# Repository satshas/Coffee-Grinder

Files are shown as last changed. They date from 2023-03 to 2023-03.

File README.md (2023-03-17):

# Coffee-Grinder
An Open Source Coffe Grinder made with a Pop-up Factory and Open Hardware Fab Lab Machines
<br>
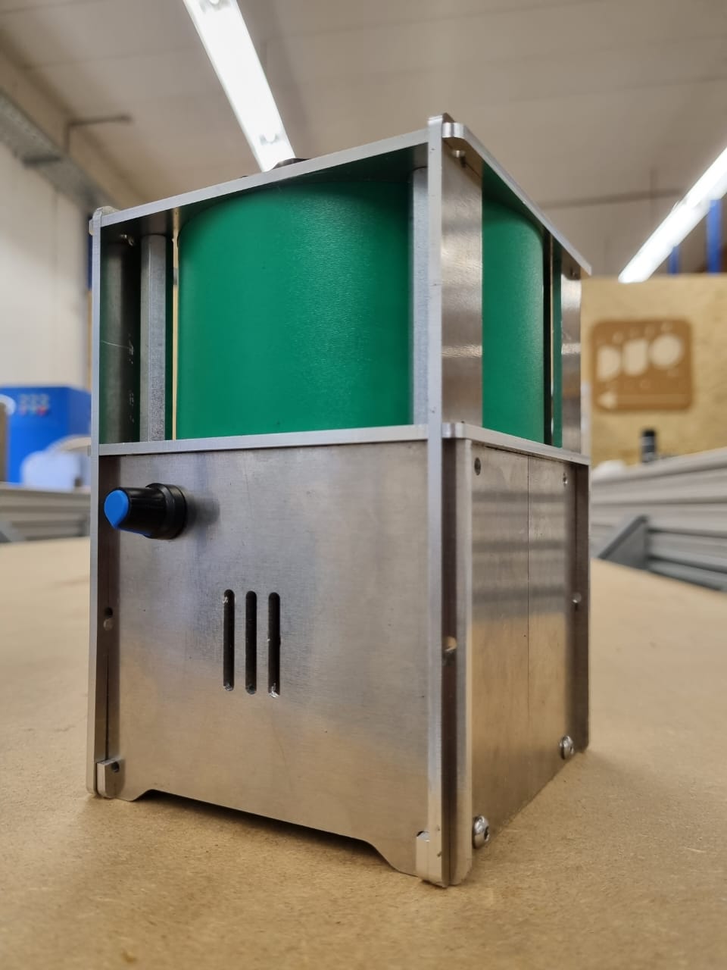
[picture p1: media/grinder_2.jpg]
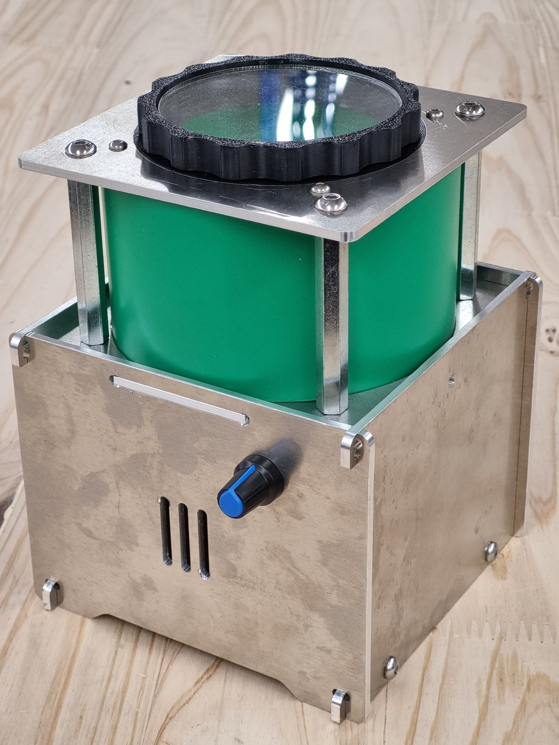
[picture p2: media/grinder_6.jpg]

<div align="center">      Version 1  |  Version 2</div>
<br>

# Specifications

- CNC milled 3mm aluminum housing
- 12V 775 DC Motor
- CNC milled grinding blade with bending
- adjustable speed
- grinding time: about 1 minute
- 3D printed screwable cap
- laser cut polypropylene grinding area

# Assembly Instructions V2

## **Sub Assembly A: grinding chamber**
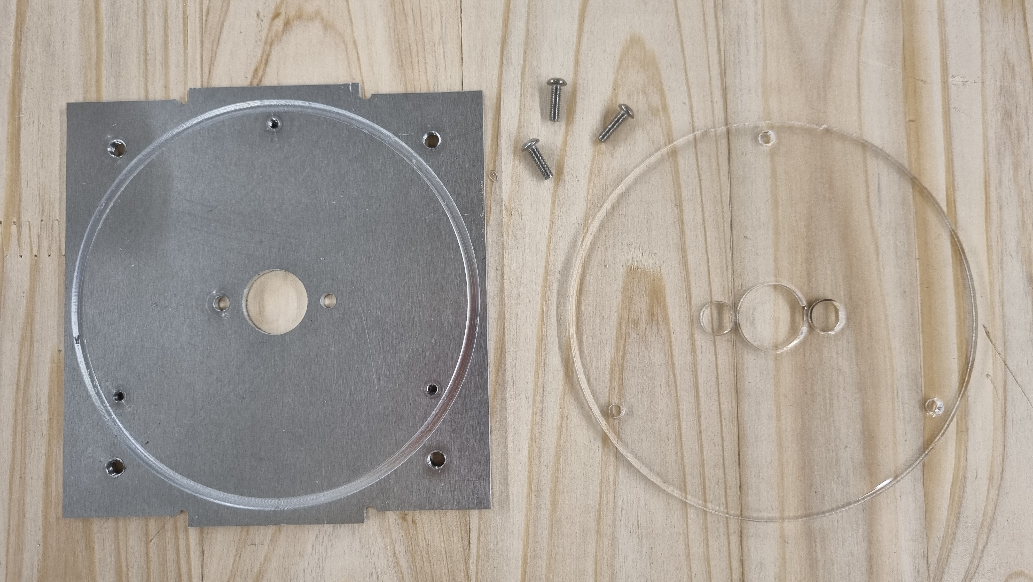
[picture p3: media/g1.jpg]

<br>
1. Attach big acrylic disc to aluminium square with 3 central holes using M3x10mm bolts (this assabled part will be refered in the next steps as "botom of the grinding chamber").
<br><br>
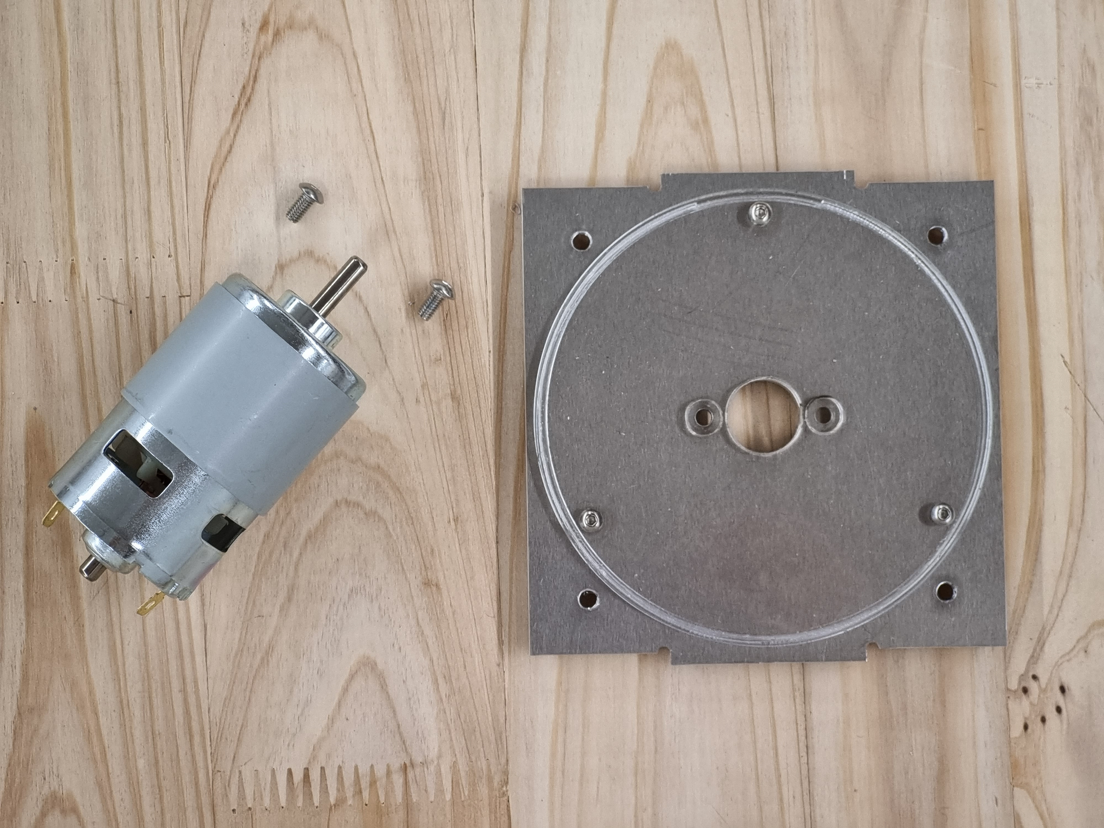
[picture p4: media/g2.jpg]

<br>
2. Attach the DC motor to the bottom ginding chamber using 2 M4x10 bolts.
<br><br>
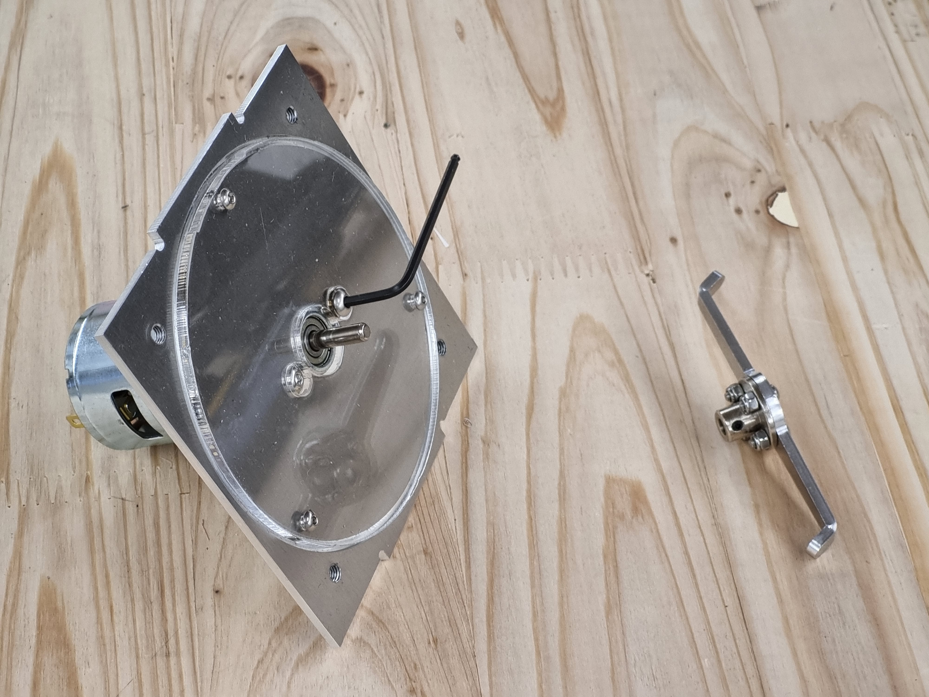
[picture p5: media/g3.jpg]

<br>


<div align="center">The blade should be assembled to the motor coupler using 4 M3x10mm bolts and 4 M3 Locknuts.<br>To secure the motor coupler to the motor´s shaft you need to tighten  the 2 setscrews.</div>
<br><br>
3. Attach the male part of the M5x60mm standoffs to the bottom ob the grinding chamber.<br><br>
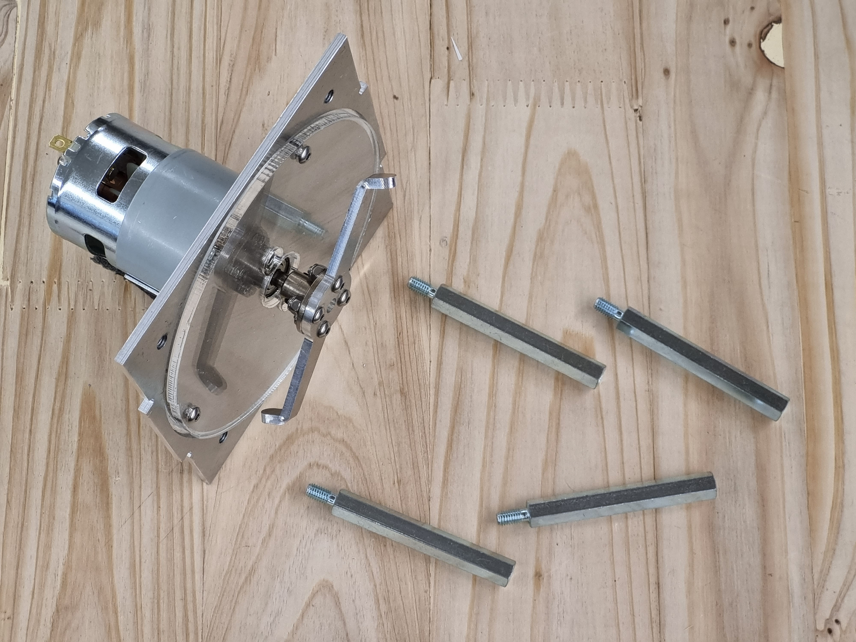
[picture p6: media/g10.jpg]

<br>
5. Place the 3D printed cap to the square aluminum piece with the big hole in the center so that the wider part of the printed part fits with the circle slot. (this assembled part will be refered as "top of the grinding chamber" in the next steps).<br><br>
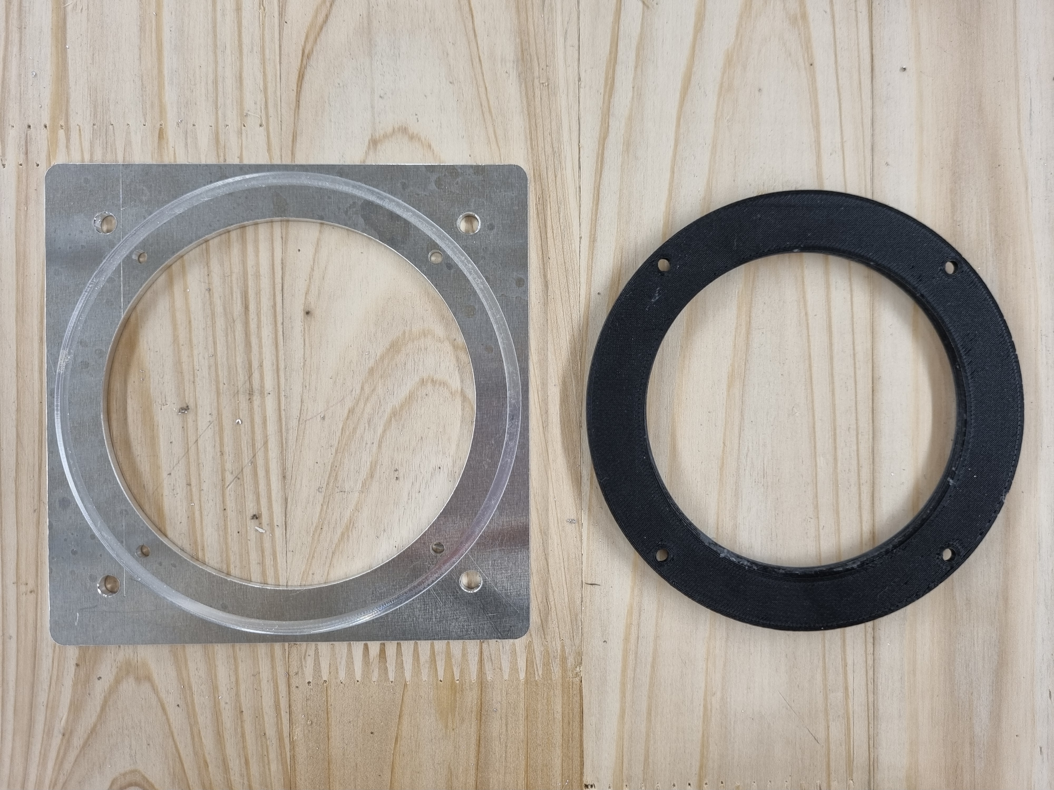
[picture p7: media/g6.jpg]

<br>
For this step, you will need four M3x10mm and four M3 locknuts.<br><br>
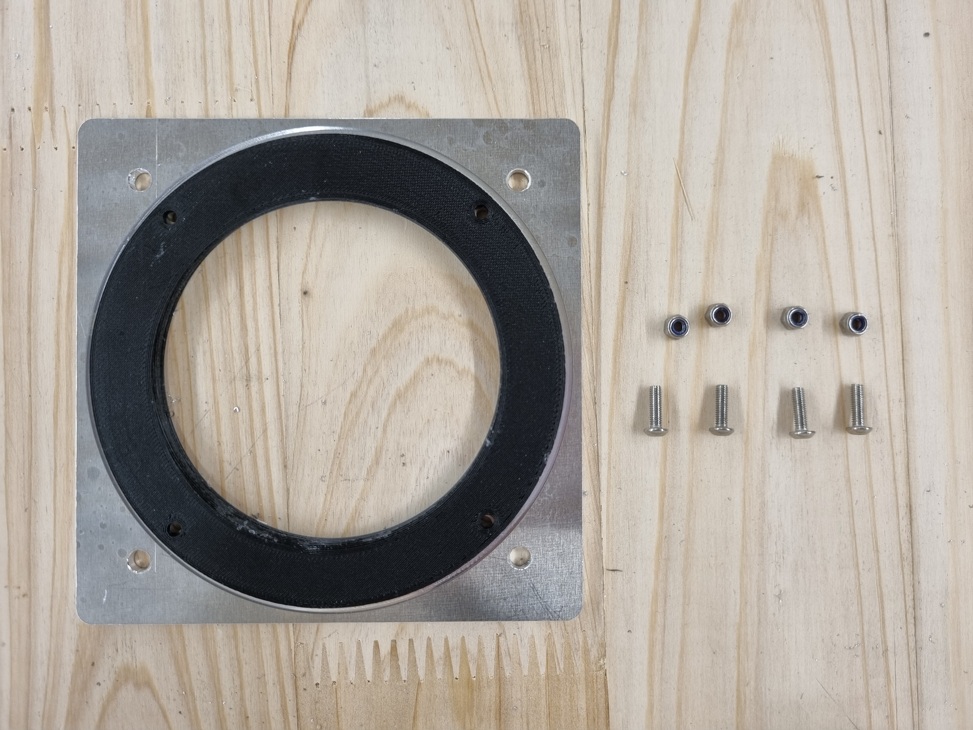
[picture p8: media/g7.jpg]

<br>
5. Place the bolts so that their heads are opposite to the side of the circle slot.<br><br>
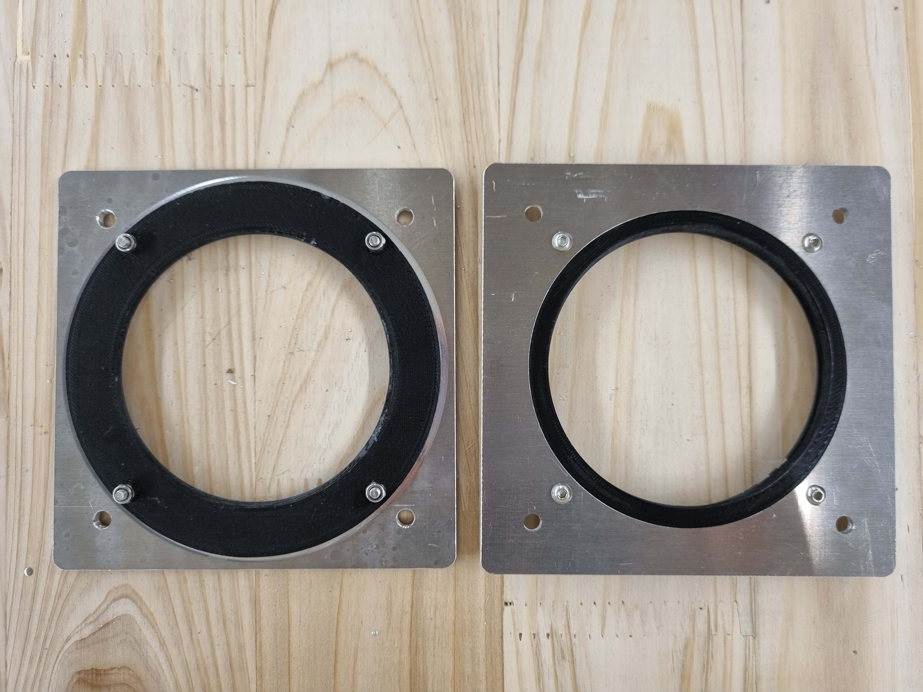
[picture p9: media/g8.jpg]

<br>
DO NOT overtighten, otherwise the 3D printed part will wrap.<br><br>

<br>
6. Attach the top of the grinding chamber and fasten it to the female part of the standoffs with 4 M5x12mm bolts.<br><br>
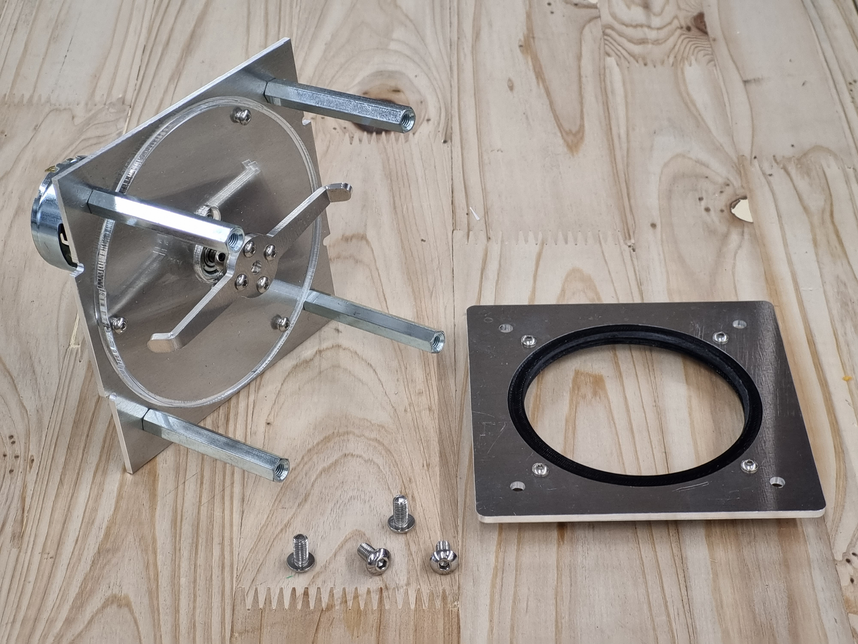
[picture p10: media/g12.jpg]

<br>
Do not tighten the bolts. The space between the top and the bottom part of the chamber should be enough to fit the green polypropilen stripe.<br><br>
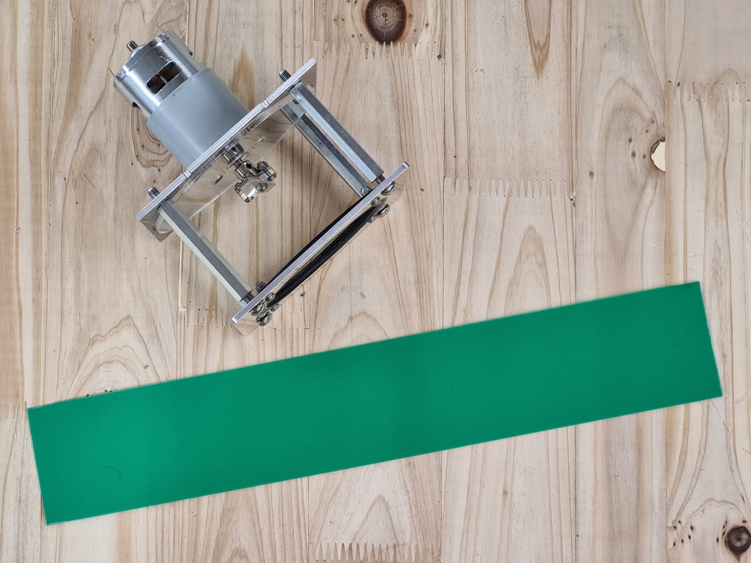
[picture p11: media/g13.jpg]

<br>
7. Roll the green polypropilen stripe to form an overlaped cilinder inside the standoffs and fit it to the bottom and top circle pockets.<br><br>
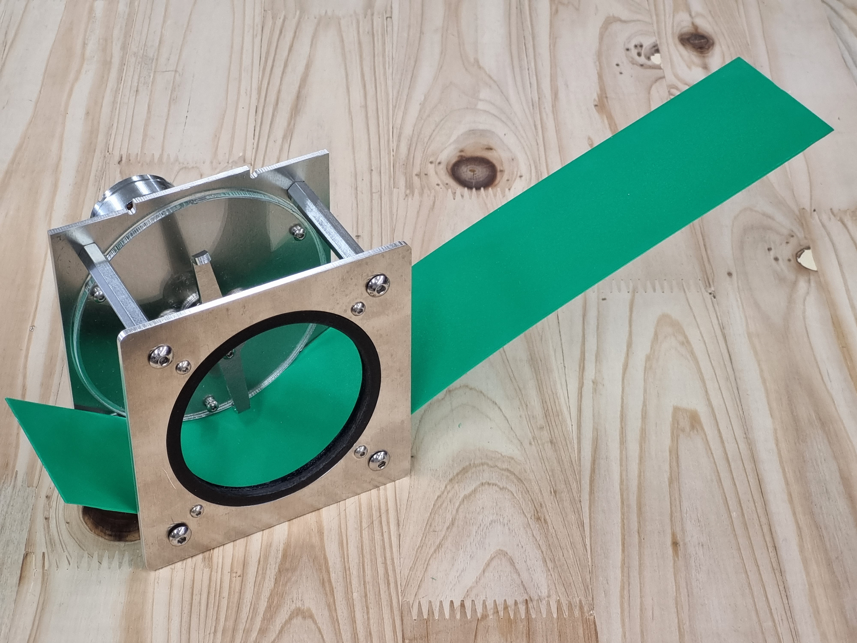
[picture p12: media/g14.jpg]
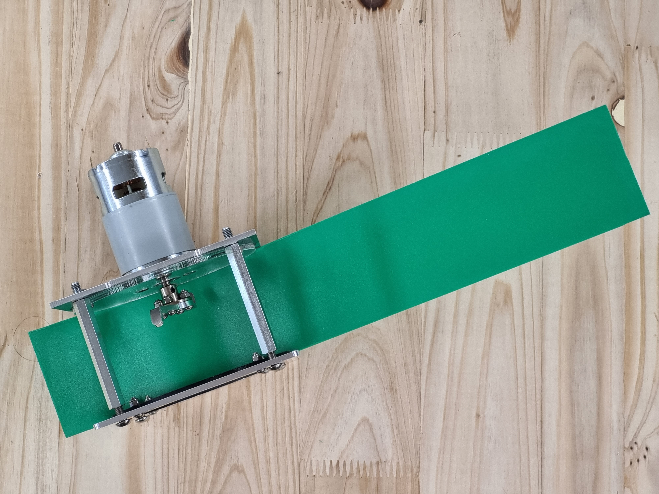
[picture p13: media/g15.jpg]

<br>
8. Place the overlaped part in the pocket next to the centered bolt in the acrylic disc.<br><br>
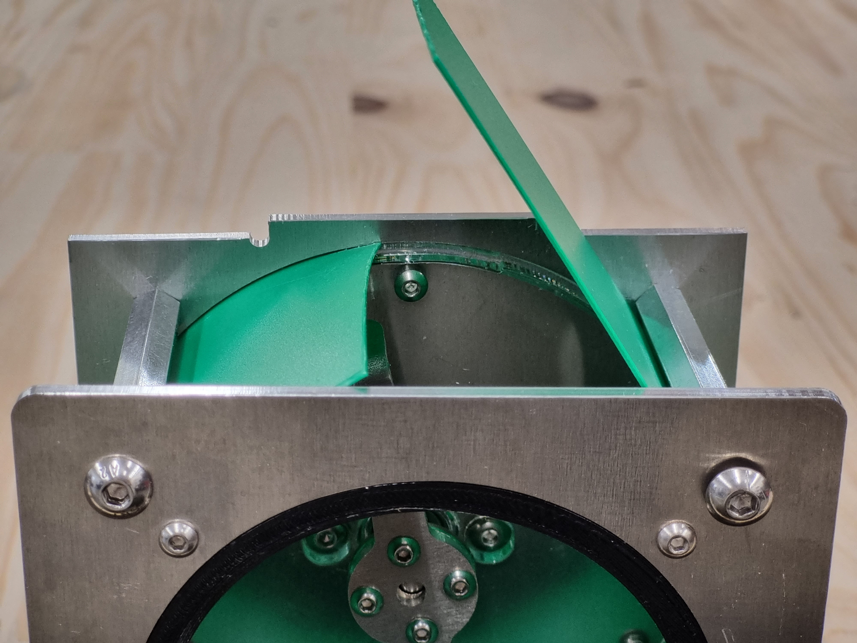
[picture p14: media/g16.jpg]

<br>
9. Rotate the formed cylinder so the overlaped part remains behind one of the standoffs.<br><br>
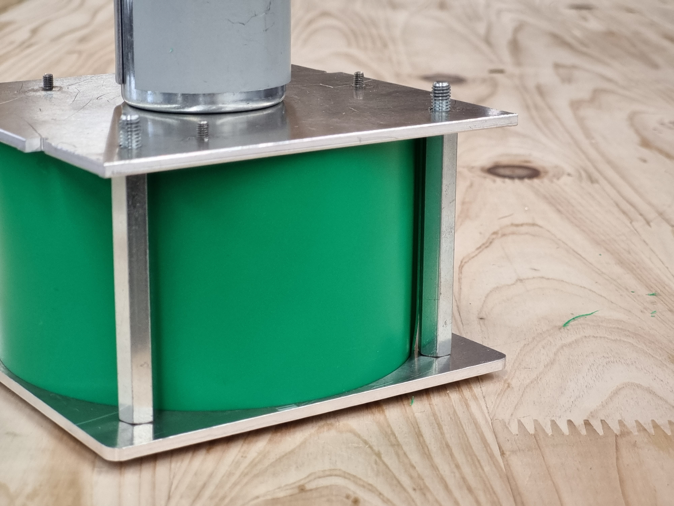
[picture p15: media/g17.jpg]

<br>
10. While having the grinding chamber upside down place the front and back aluminium plates. The one with de centered hole is where the back, where the DC barrel jack connector goes.<br><br>
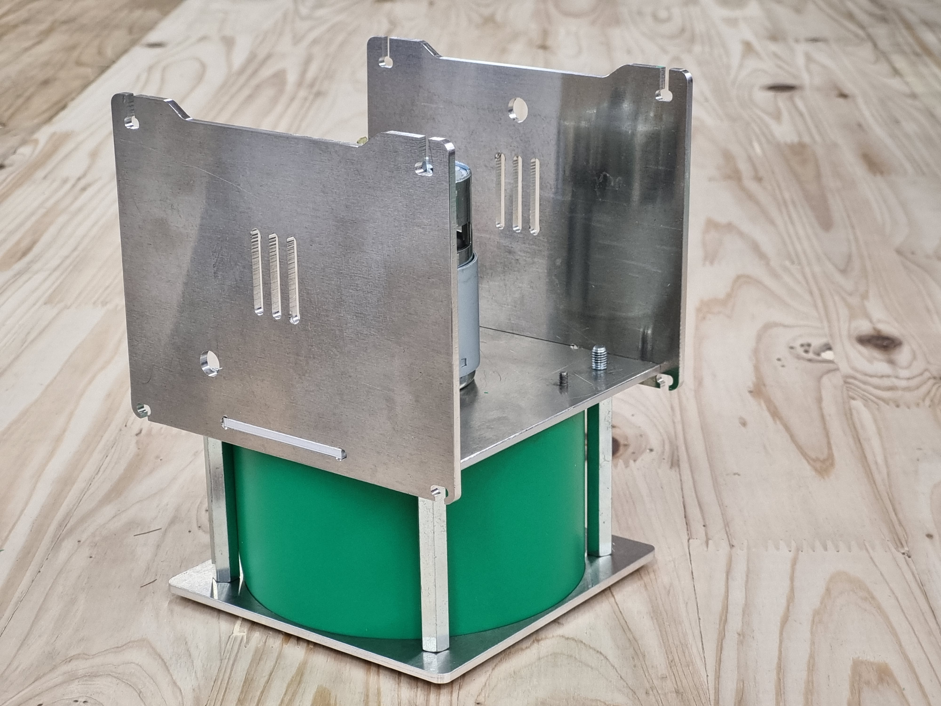
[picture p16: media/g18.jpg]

<br>
11. Flip the assembly and slide the two side aluminium plates from above.<br><br>
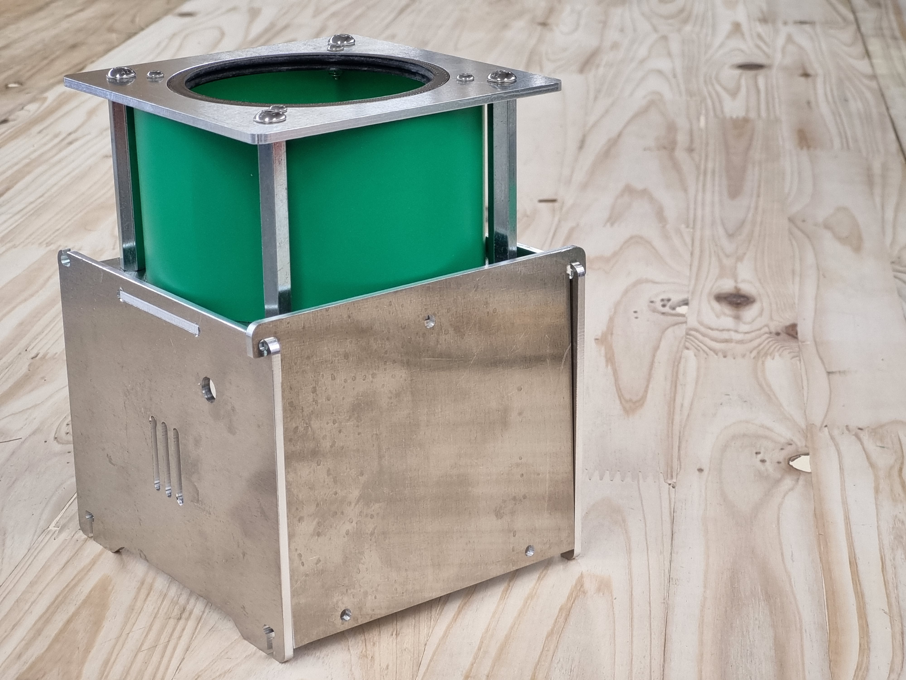
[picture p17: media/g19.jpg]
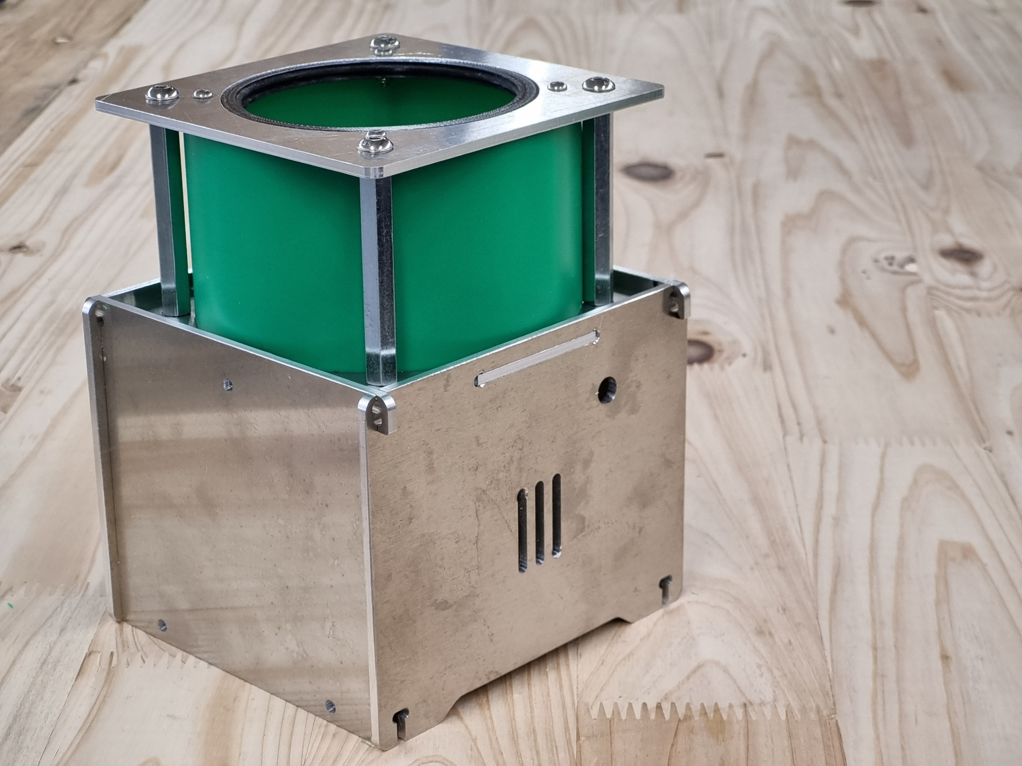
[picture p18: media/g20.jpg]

<br>
12. Slide the 2 aluminium reteiners them in to their corresponding notches and secure them to the side plates using 4 M4x10mm bolts.<br><br>
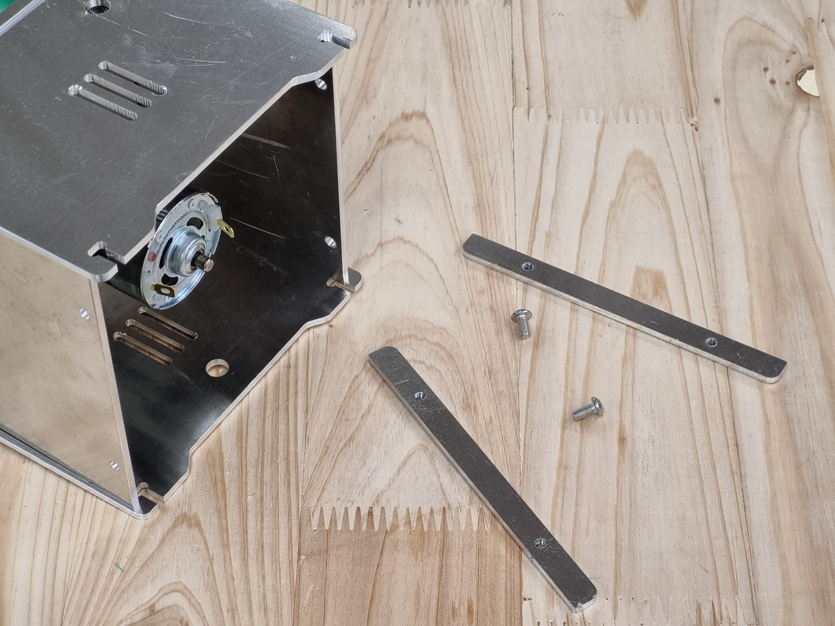
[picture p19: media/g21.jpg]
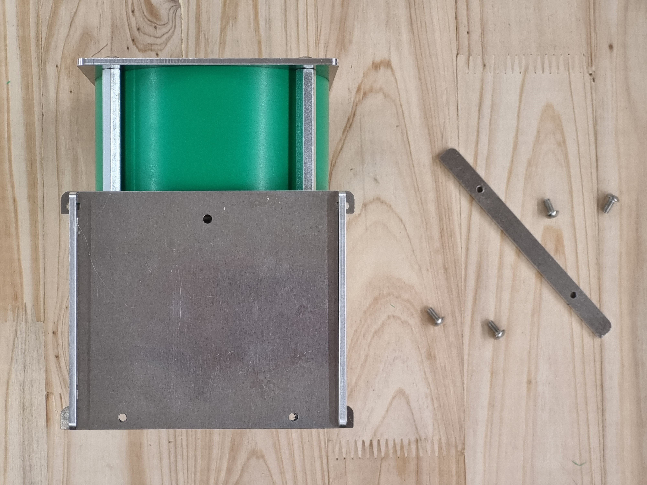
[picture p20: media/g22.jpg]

<br>
13. Attach the DC barrel jack connector to the back plate, secure it with the provided nut.<br><br>
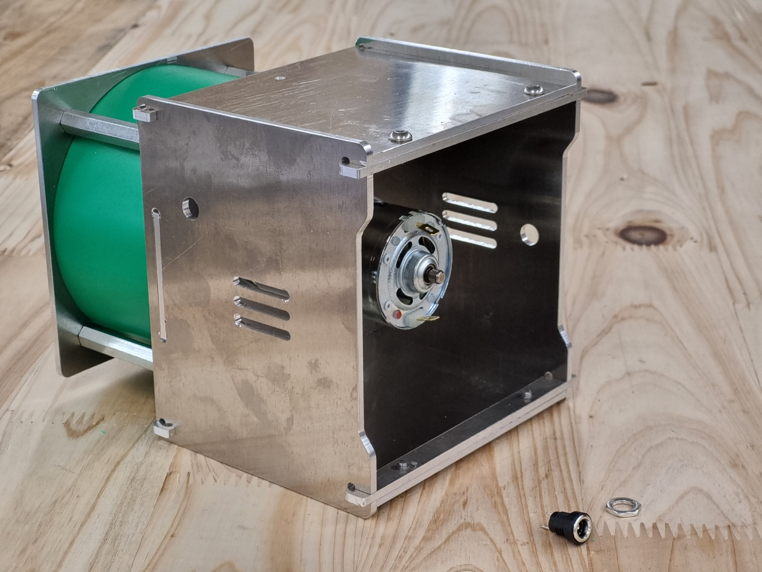
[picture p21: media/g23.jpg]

<br>
14. Prepare the electronic parts. Cables, connectors and controller board.<br><br>
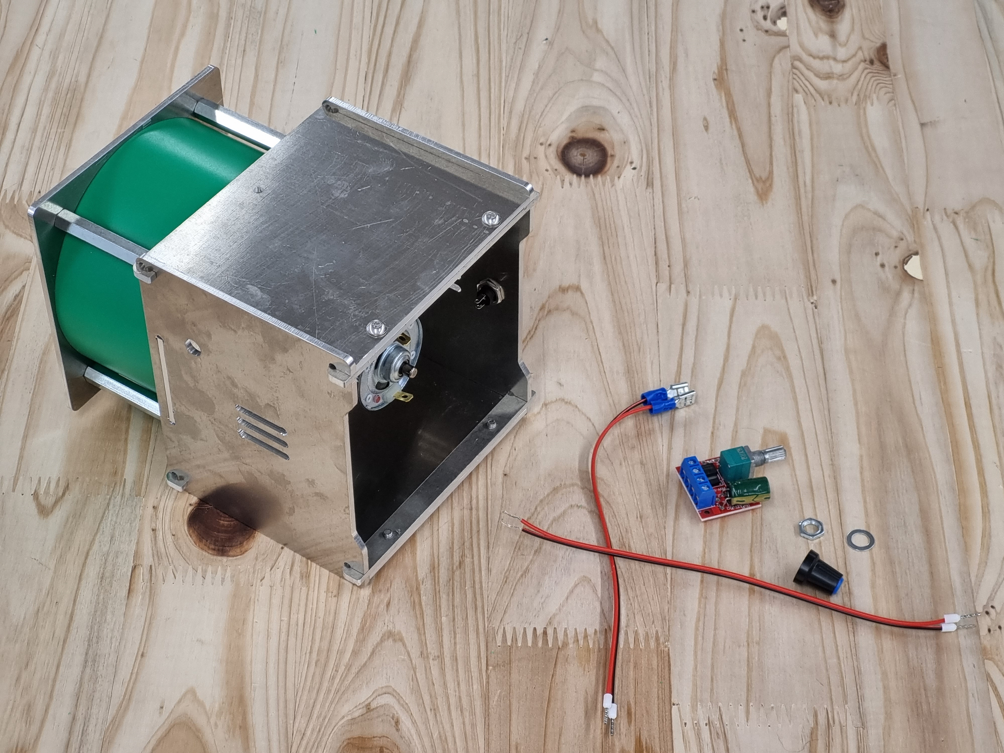
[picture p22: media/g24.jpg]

<br>
15. Make the 4 connections and check the position for the motor connection and the power connection.<br><br>
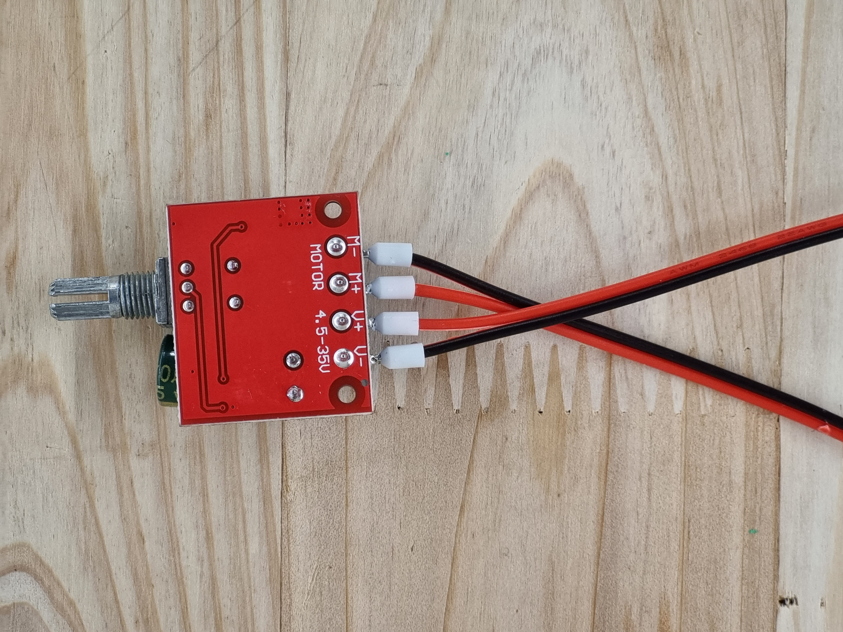
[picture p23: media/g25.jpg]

<br>
16. Attach the controller board the the front aluminium plate by srewing the shaft of the board through the hole located in the top right (or left) of the plate, secure it with the provided nut.<br><br>
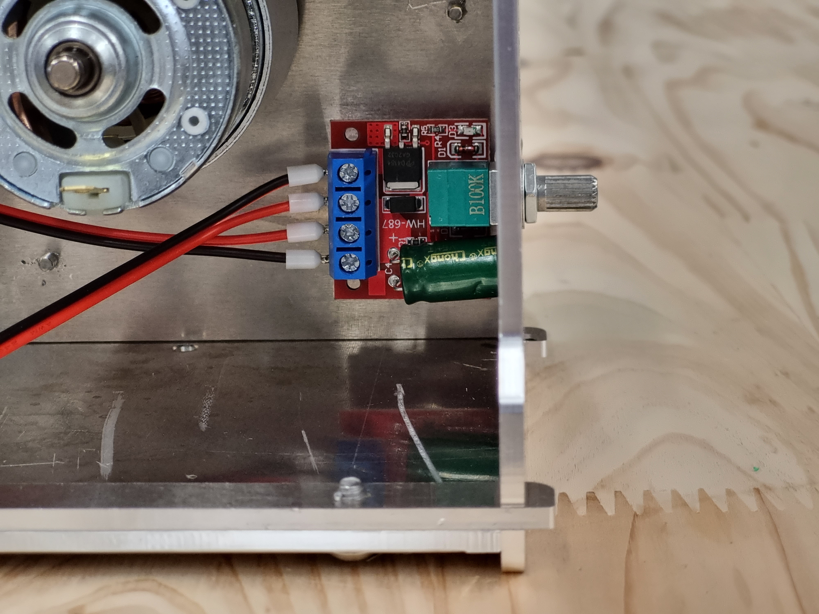
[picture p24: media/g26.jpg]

<br>
17. Connect the cables to the motor and DC jack checking wich ones correspond to ground and vcc for each.<br><br>
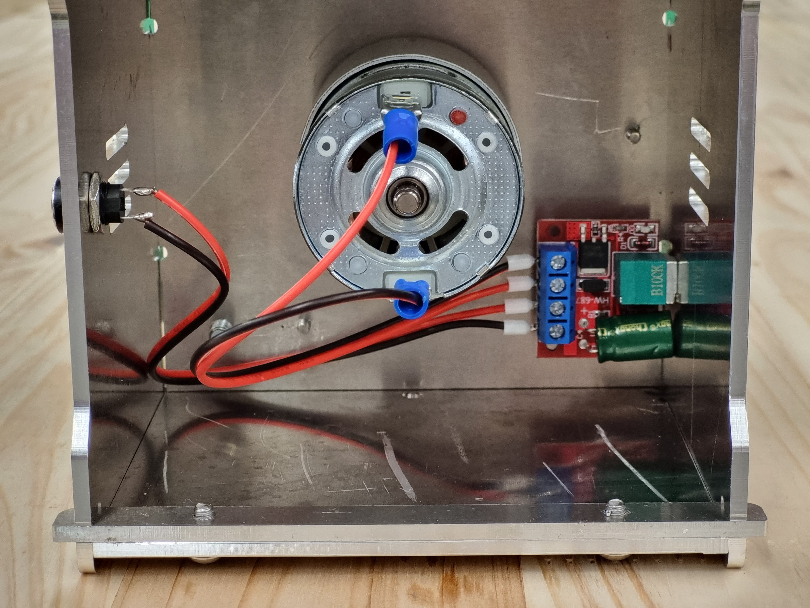
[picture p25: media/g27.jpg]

<br>
18. Place the cap.<br><br>
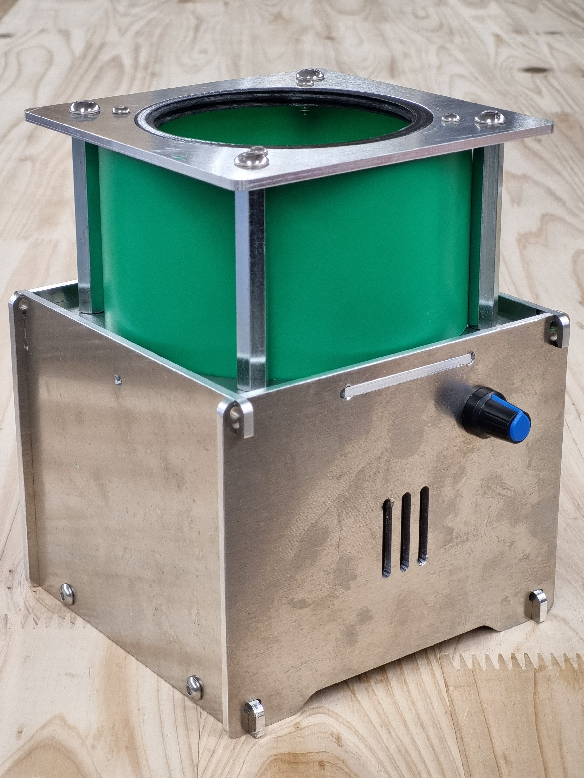
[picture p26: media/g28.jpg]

<br>
19. Preesfit attachment of the small acrylic disc to the top 3D printed cap.<br><br>
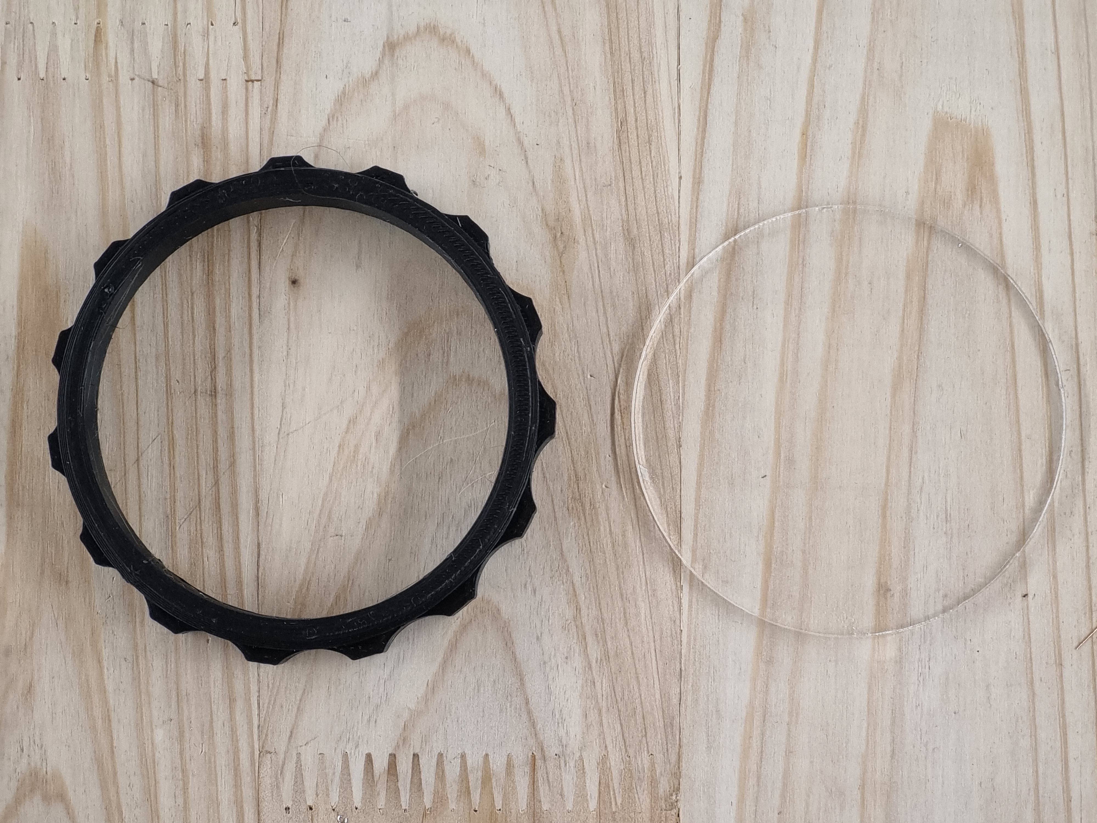
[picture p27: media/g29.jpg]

<br>
20. Place the big cap.<br><br>
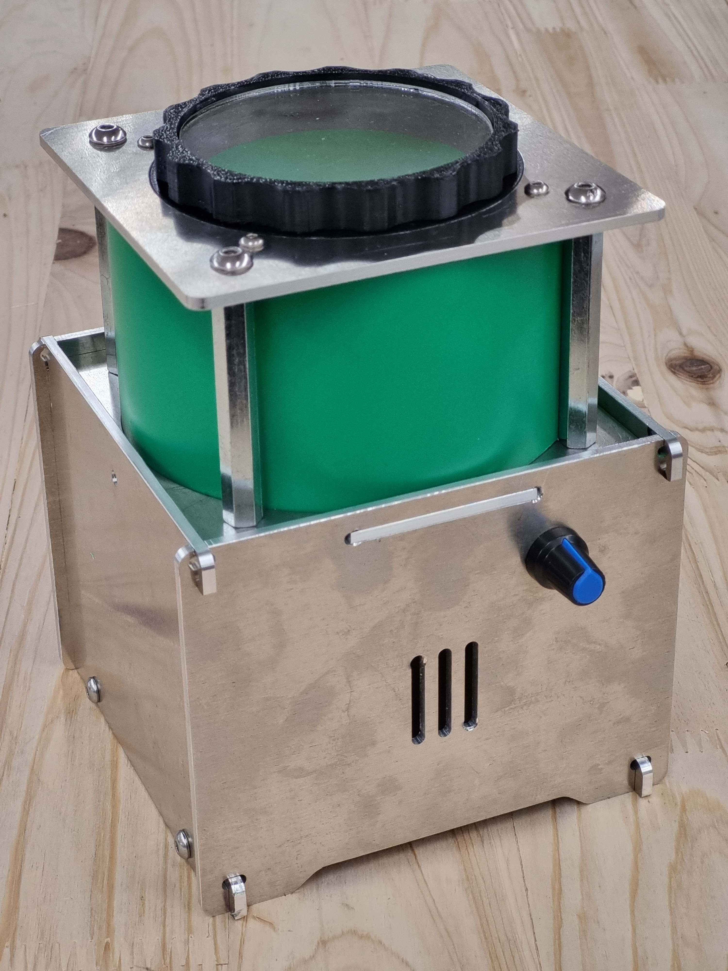
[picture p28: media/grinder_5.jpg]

<br>
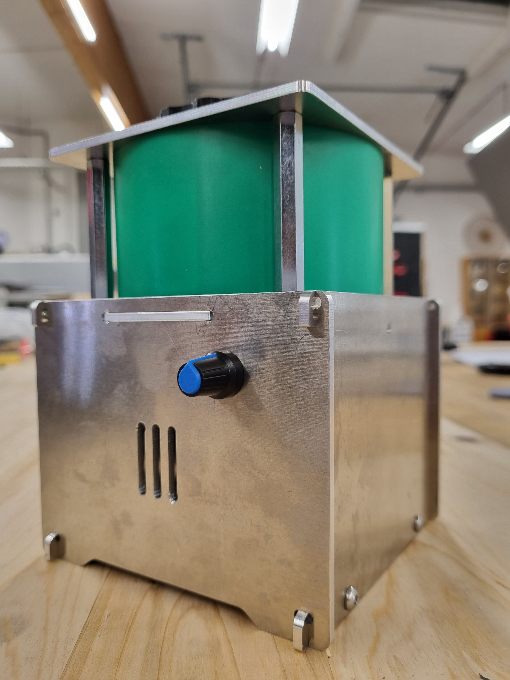
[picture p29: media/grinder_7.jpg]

<br>

<br>



<br>

Author
--

The Coffe Grinder has been designed and built by **[InMachines Ingrassia GmbH](https://www.inmachines.net/)**.



<br>

Coffe Grinder design by:
- **[Wilhelm Schütze](http://fabacademy.org/archives/2015/sa/students/schutze.wilhelm/index.html)**

Contact
--

- daniele@inmachines.net
- [https://www.inmachines.net/](https://www.inmachines.net/)

License
--

The Coffe Grinde design, CAD and PCB files, BOM, settings and relative files are are released under the following open source license:

- CERN Open Hardware Licence Version 2 Weakly Reciprocal - **[CERN-OHL-W](LICENSE_CERN_OHL_W_V2.txt)**

The Coffe Grinder documentation, pictures and presentation text of this repository are released under the following license:

- Creative-Commons-Attribution-ShareAlike 4.0 International - **[CC BY-SA 4.0](LICENSE_CC_BY_SA_4.0.txt)**

Download
--

### V2 CAD files

- **[STEP file](cad/coffeegrinderV2.step)**
- **[FUSION file](cad/coffeegrinderV2.f3z)**

### V1 CAD files

- **[STEP file](cad/_coffee_grinder_v2.step)**
- **[FUSION file](cad/coffeegrinderv1.f3z)**
- You can check the version 1 exploded view in previous commits.

### BOM

- **[.xlsx file](coffee_grinder_BOM.xlsx)**
- **[.ods file](coffee_grinder_BOM.ods)**

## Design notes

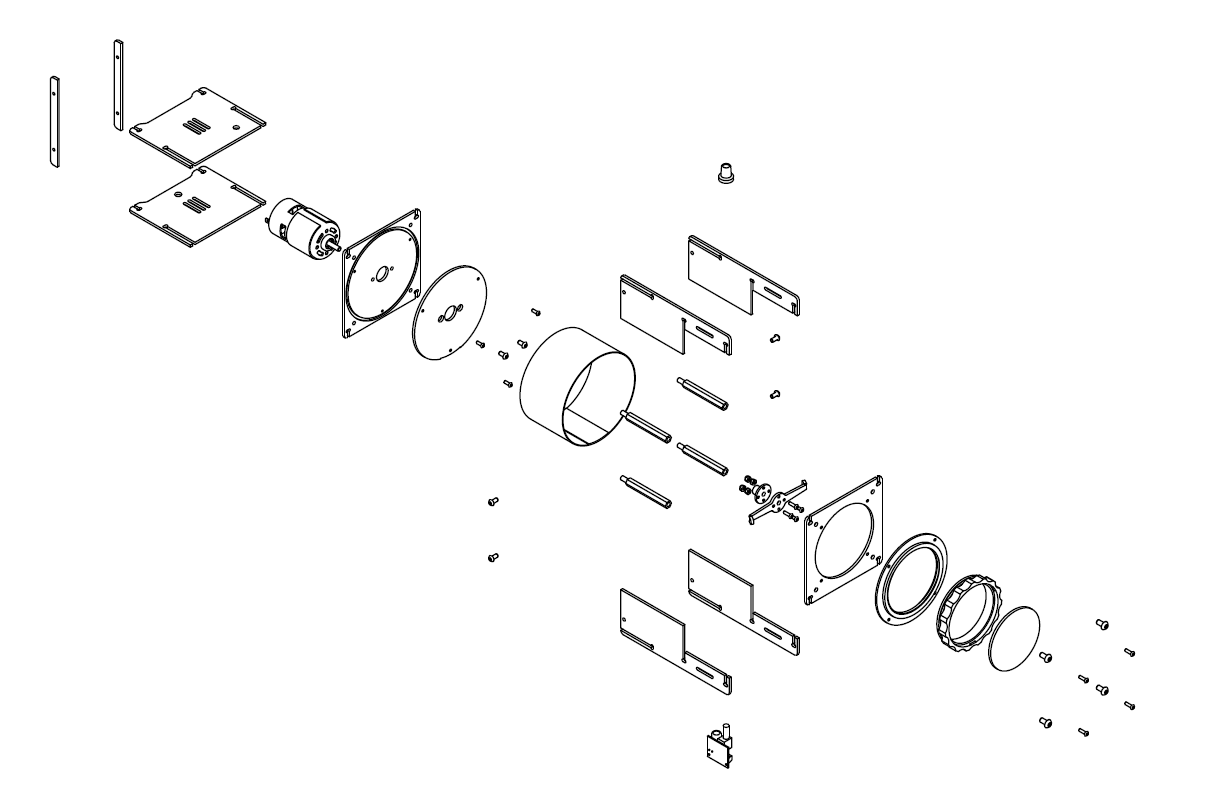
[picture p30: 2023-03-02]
media/exploded_view.png

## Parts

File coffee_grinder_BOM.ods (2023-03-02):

Item | Description | Qty | Price unit | Price total | Coment | Link
DC Motor | 775 Dc Motor | 1 | 23 | 23 | with 5mm shaft | https://www.amazon.de/12V-36V-3500-9000-Bearing-Electronic-Component/dp/B08NVSQ8N4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
Motor shaft coupler | 5mm iner shaft coupler | 1 | 10 | 10 | comes in a 4 pack | https://www.amazon.de/-/en/sourcing-Inner-Diameter-Motor-Coupling/dp/B094NZJ8DJ
Motor speed controller | 5A speed controller | 1 | 8 | 8 | comes in a 4 pack | https://www.amazon.de/dp/B09KNKQ7GJ?s=industrial&sp_csd=d2lkZ2V0TmFtZT1zcF9kZXRhaWw
DC barrel jack | 5.5mm x 2.1mm | 1 | 7 | 7 | comes in a 12 pack | https://www.amazon.de/-/en/ThreeBulls-Female-Mounting-Connector-Socket-12-pieces/dp/B01N8VV78D
External power supply | 12v 5A | 1 | 15.4 | 15.4 | sames as for the scanner and vinyl cutter | https://www.amazon.de/Leicke-Netzteil-Bildschirm-Festplatten-Pico-PSU/dp/B001W3UYLY?hvadid=308634037828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
button head bolt | M5 x 10mm | 1 | 12.2 | 12.2 | 100 pack | https://www.ebay.de/itm/162273774368?epid=2005340391&hash=item25c8454b20:g:VqwAAOSwnJVZnUIE
button head bolt | M4 x 8mm | 1 | 9.7 | 9.7 | 100 pack, we have some | https://www.ebay.de/itm/371784247972?hash=item5690116aa4:g:mXEAAOSwdrhZnFf8
button head bolt | M3 x 8mm | 1 | 6.6 | 6.6 | 100 pack | https://www.ebay.de/itm/371784247897
button head bolt | M3 x 10mm | 1 | 7.5 | 7.5 | 100 pack | https://www.ebay.de/itm/371784247897
button head bolt | M3 x 16mm | 1 | 8.5 | 8.5 | 100 pack | https://www.ebay.de/itm/371784247897
Locknut | M5 | 1 | 5.8 | 5.8 | 100 pack, to re-stock | https://www.ebay.de/itm/371582274398?hash=item5684078b5e:g:AI0AAOSwB31ZnETh
Locknut | M3 | 1 | 5.6 | 5.6 | 100 pack, to re-stock | https://www.ebay.de/itm/371582274159?hash=item5684078a6f:g:ATcAAOSw0GJZnETM
Standoff / spacer | M5 x 60mm | 1 | 52.5 | 52.5 | 100 pack, we have some | https://www.ebay.de/itm/134376871188
4mm aluminum plate | 500x350x4mm | 1 | 37 | 37 | for each, maybe is better to buy bulk | https://www.amazon.de/-/en/Aluminium-Sheet-ALMg3-Including-Measure/dp/B07XF6CB7M?s=industrial
3mm Acrilyc sheet | 600x400x3mm | 3 | 12 | 36 | for all 20 machines | https://www.amazon.de/dp/B08L3V215Z?ref=ppx_yo2ov_dt_b_product_details&th=1
0.7mm PET sheet | 600x400x0.7mm | 2 | - | - | we have them
3D printing filament | PLA 1.75mm black | 1 | 25 | 25 | esun brand? | https://www.amazon.de/-/en/eSun-Filament-PLAPlus-Printer-Black/dp/B09GCNV3W7

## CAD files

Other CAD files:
cad/coffeegrinderV2.f3z
cad/coffeegrinderv1.f3z

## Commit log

2023-03-02 added cad files and exploded view
    [coffe_grinder_v2.f3z]
2023-03-02 added BOMs
    [coffee_grinder_BOM.ods, coffee_grinder_BOM.xlsx]
2023-03-02 Update README.md
    added details to BOM
2023-03-02 Update README.md
    added assembly instructions
